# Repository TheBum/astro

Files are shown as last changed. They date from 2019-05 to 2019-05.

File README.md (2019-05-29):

# Description

This is a package that works with a Raspberry Pi Zero W and provides both a Wifi-to-serial interface and GPS time and location information to a telescope mount. It is based upon the [Raspberry PI wireless Telescope Control][proj-url] project.

Time and location are transferred to the hand controller over USB. The transfer happens automatically when the USB cable between the Pi and the hand controller is plugged in. The display will provide a message when time and location uploads are in progress.

This has been tested with a Celestron Advanced VX equatorial mount with its regular hand controller and the hand controller from a StarSense Auto Align unit.

# Hardware

The included case files assume you're using the following components:  
  
* Raspberry Pi Zero W with a 2x6 header soldered to the top GPIO pads on the front of the board  
* SSD1306 128x32 pixel I2C OLED display (e.g. [this Maker Focus display][oled-url]) with a header soldered on so that the pins are on the back of the board  
* 12V-to-5V converter (e.g. [Pololu D24V10F5][conv-url]) attached to empty GPIO pads at the bottom of the front of the board with double-sided tape  
* Single-board GPS module (e.g. [Gowoops GPS-NEO-6M-001][gps-url] or similar form factor) with a header soldered on so that the pins are on the chip side (not the antenna side)
* Keystone CAT3/RJ12 6P6C modular jack with a maximum body width of 20mm (e.g. [Shaxon BM303W610-B][jack-url])
* Wire and header plugs to electrically connect the components; a 2-pin connector for the power coming from the keystone jack is recommended for ease of assembly
* A case; 3D model files are provided in the [case][case-dir] folder in Fusion 360, STEP, and STL formats for design tweaks and 3D printing

The diagram below shows how I wired up the Pi, OLED, and GPS. I used two 4-position single row female connectors (denoted by the green and red boxes; note that one position in the OLED connector is empty) and wired both modules' Vcc into pin 1 on the Pi using a single terminal and heat shrink tubing (denoted by the cyan box; the terminal was too full to fit in a 1-position housing). I used a header only long enough for the number of GPIB rows affected (six), which allows the header and connectors to fit into the open area designed into the case and the rest of the Pi to lie flat against the posts.
Wiring diagram
The power from the voltage converter is fed into the solder pads on the bottom of the Pi, under the USB power connector, to take advantage of the fuses in the USB power feed.
Wiring diagram back

# Software Installation

After setting up the wifi in the Pi (editing the wpa_supplicant.conf file), software installation is simple:

1. Download the distribution from GitHub either via a git clone or as a zip file. If downloaded as a zip, unzip it. You will now have an "astro" folder.  
2. Run the following commands:  

	`cd <path-to-astro-folder>`  
	`sudo cp etc /`  
	`sudo cp usr /`  
3. Follow the instructions in the [base project][proj-url] to update the Pi's OS and install/configure the ser2net and gpsd services. The
autohotspot service will be installed by the action in step 2, but if you need to make changes to the network name or WPA passphrase for the hotspot, do it now.
4. Enable the services that were installed in step 2. The sethctimeloc enable will complain of a lack of an installation config: just ignore it because installation is done when the USB cable is plugged in.  

	`sudo systemctl enable autohotspot`  
	`sudo systemctl enable forcetimeupdate`  
	`sudo systemctl enable sethctimeloc`  
	`sudo systemctl enable gpsdisplay`  

Then just reboot and you should have a fully operational system.

[proj-url]: https://hackaday.io/project/162681-raspberry-pi-wireless-telescope-control
[oled-url]: https://smile.amazon.com/gp/product/B079BN2J8V/
[conv-url]: https://www.pololu.com/product/2831
[gps-url]: https://smile.amazon.com/gp/product/B01AW5QYES/
[jack-url]: https://smile.amazon.com/Shaxon-Cat3-Keystone-White-BM303W610-B/dp/B00J8D0LT0/  
[case-dir]: ./case

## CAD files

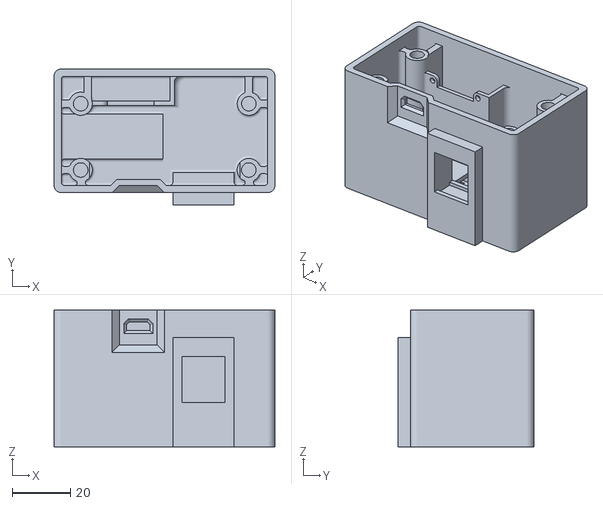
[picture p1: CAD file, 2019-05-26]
case/Box.stl
76.0 x 46.8 x 47.0

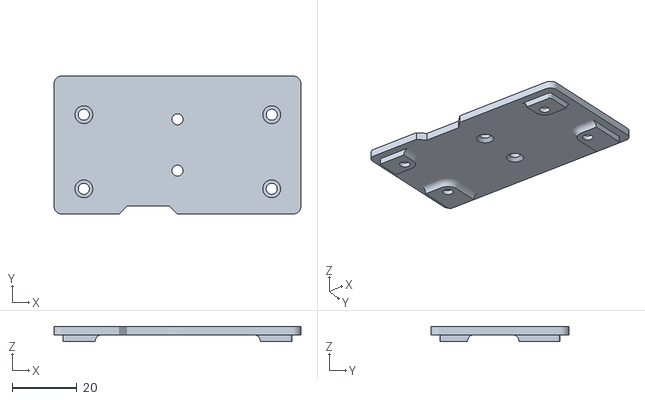
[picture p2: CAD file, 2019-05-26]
case/Lid.stl
76.0 x 42.5 x 4.50

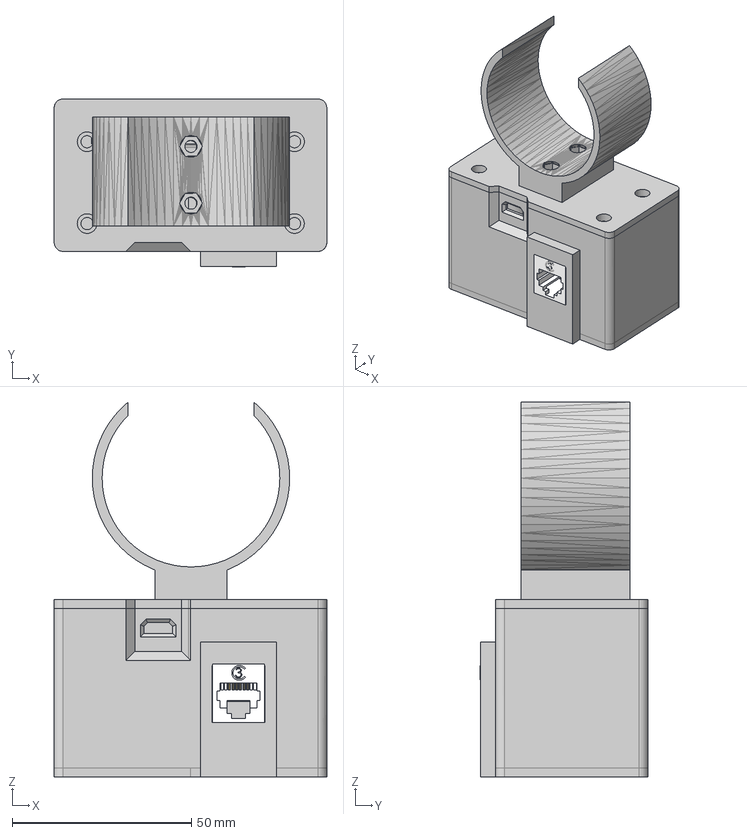
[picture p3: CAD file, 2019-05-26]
case/GPS-Wifi Case.step
76.0 x 46.9 x 104.5 mm
CAT3 Tooless IDC Keystone Jack
Lid
Clamp

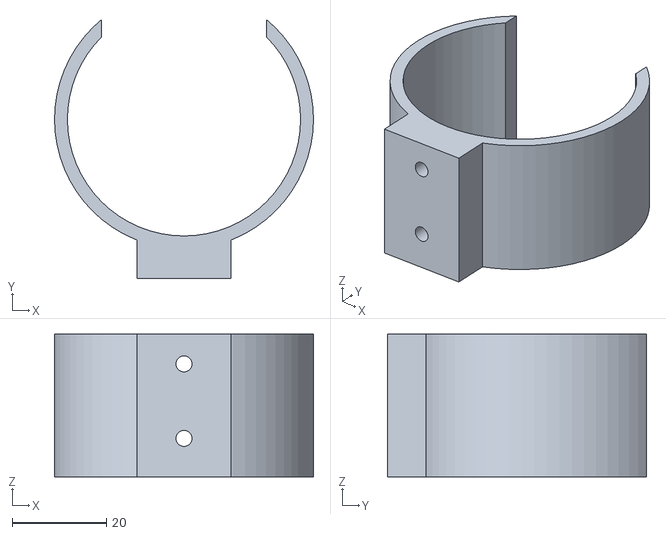
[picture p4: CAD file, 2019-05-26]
case/Clamp.stl
55.0 x 55.0 x 30.3

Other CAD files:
case/GPS-Wifi Case.f3z

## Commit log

2019-05-26 Files for the case that holds the boards/modules
    [Box.stl, Clamp.stl, GPS-Wifi Case.f3z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]
2019-05-29 Added the wiring diagram to the README file
2019-05-29 Added a power connection diagram
